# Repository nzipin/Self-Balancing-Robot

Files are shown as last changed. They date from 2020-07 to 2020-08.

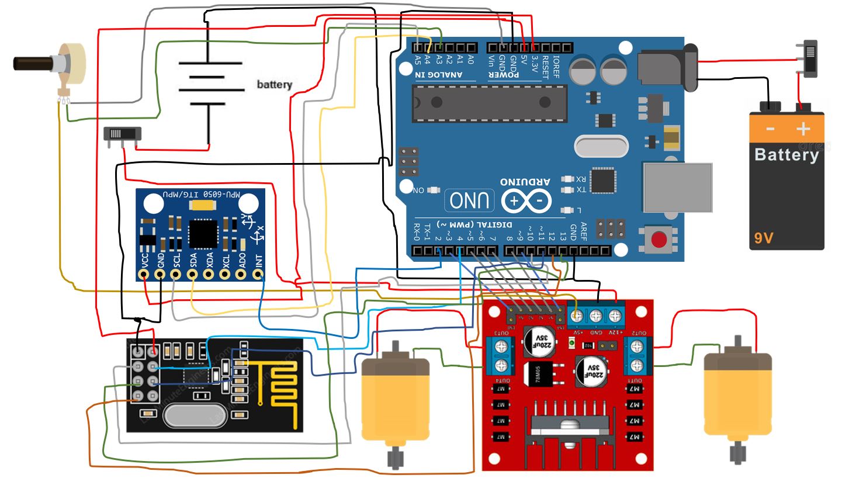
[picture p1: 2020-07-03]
Electronics/Wiring diagram.JPG

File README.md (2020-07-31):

# Self-Balancing-Robot
All artifacts from a 2 wheel balancing robot project as seen on YouTube  
https://www.youtube.com/watch?v=M7D-TyRbdDE&list=PLmEi2OoxXIQ88akwk1nRoXV6LqhXQp3kH  

**Full Parts List**  
*Mechanics:*  
- 1x verntech 4pcs 300mm T Type Aluminum Profile Extrusion https://www.amazon.com/gp/product/B07KB1HD8T/ref=ppx_yo_dt_b_asin_title_o03_s04?ie=UTF8&psc=1  
- 1x Polycarbonate Clear Plastic Sheet 12" X 18" X 0.0625" (1/16") https://www.amazon.com/gp/product/B07MQTDF4R/ref=ppx_yo_dt_b_asin_title_o03_s03?ie=UTF8&psc=1  
- 1x M3 T Slot Nut Hammer Head Fastener Nut https://www.amazon.com/gp/product/B07SDFCTD4/ref=ppx_yo_dt_b_asin_title_o03_s05?ie=UTF8&psc=1  
- 1x 20 Pcs M3 Stainless Steel 304 Hex Socket Head Cap Screws Nuts https://www.amazon.com/gp/product/B07HQ5761L/ref=ppx_yo_dt_b_asin_title_o03_s02?ie=UTF8&psc=1  
- 2x 156:1 Metal Gearmotor 20Dx44L mm 12V CB with Extended Motor Shaft https://www.pololu.com/product/3492  
- 1x Dagu Wild Thumper Wheel 120x60mm Pair with 4mm Shaft Adapters https://www.pololu.com/product/1555  
- 1x Generic plastic coat hanger  

*Electronics:*  
(Robot):  
- 1x Arduino Uno https://www.amazon.com/ELEGOO-Board-ATmega328P-ATMEGA16U2-Compliant/dp/B01EWOE0UU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  
- 1x Silicon Wire https://www.amazon.com/gp/product/B07G2HFCS1/ref=ppx_yo_dt_b_asin_title_o06_s00?ie=UTF8&psc=1  
- 1x Tegg 2PCS 9V Battery Holder with ON/Off Switch https://www.amazon.com/gp/product/B07SSY6LRB/ref=ppx_yo_dt_b_asin_title_o03_s00?ie=UTF8&psc=1  
- 1x M3 Male Female Nylon Hex https://www.amazon.com/gp/product/B07D7828LC/ref=ppx_yo_dt_b_asin_title_o03_s01?ie=UTF8&psc=1  
- 1x 4pcs NRF24L01+ Wireless Transceiver Module2.4G https://www.amazon.com/gp/product/B00LX47OCY/ref=ppx_yo_dt_b_asin_title_o03_s02?ie=UTF8&psc=1  
- 1x 5 Pcs 10K OHM Linear Taper Rotary Potentiometer https://www.amazon.com/gp/product/B01DKCUVMQ/ref=ppx_yo_dt_b_asin_title_o03_s03?ie=UTF8&psc=1  
- 1x 6cm x 4cm proto-PCB https://www.amazon.com/gp/product/B07FFDFLZ3/ref=ppx_yo_dt_b_asin_title_o03_s05?ie=UTF8&psc=1  
- 1x L298N Motor Drive Controller Board https://www.amazon.com/gp/product/B01M29YK5U/ref=ppx_yo_dt_b_asin_title_o03_s05?ie=UTF8&psc=1  
- 1x 3 x 3.7V Battery Holder https://www.amazon.com/gp/product/B071ZQ2X2T/ref=ppx_yo_dt_b_asin_title_o03_s05?ie=UTF8&psc=1  
- 1x MPU6050 3 Axis Accelerometer Gyroscope Module 6 DOF 6-axis Accelerometer Gyroscope Sensor https://www.amazon.com/gp/product/B00LP25V1A/ref=ppx_yo_dt_b_asin_title_o06_s01?ie=UTF8&psc=1  
- 3x 18650 Li-ion Battery  

(Remote Control):  

- 1x Joystick Breakout Module Game Controller for Arduino PS2 https://www.amazon.com/gp/product/B01N59MK0U/ref=ppx_yo_dt_b_asin_title_o01_s00?ie=UTF8&psc=1  
- 1x Arduino Nano https://www.amazon.com/gp/product/B07G99NNXL/ref=ppx_yo_dt_b_asin_title_o01_s01?ie=UTF8&psc=1  
- 1x  3 Pins Mini Toggle Switch https://www.amazon.com/gp/product/B01BWL7Z44/ref=ppx_yo_dt_b_asin_title_o01_s01?ie=UTF8&psc=1  
- incl. 9V battery holder, NRF24L01, and protoboard from robot electronics

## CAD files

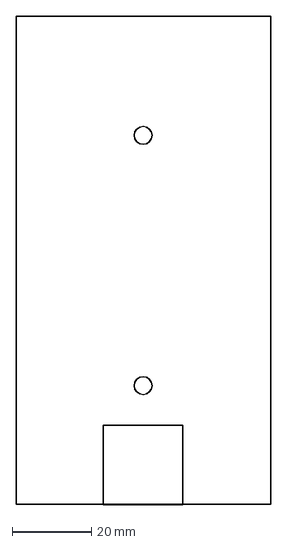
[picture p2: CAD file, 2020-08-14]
Mechanics/CAD/topplate.dxf
64.2 x 123.1 mm

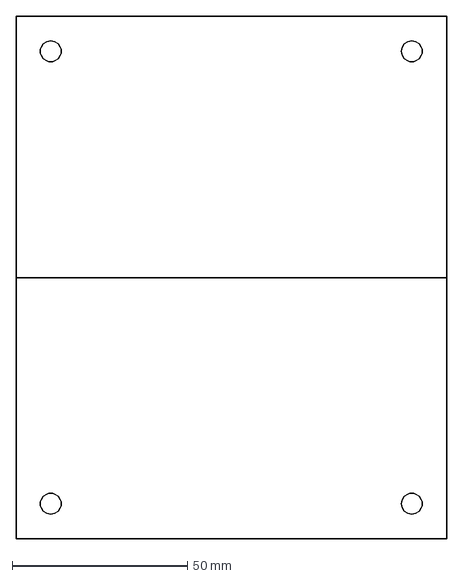
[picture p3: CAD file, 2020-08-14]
Mechanics/CAD/backplate.dxf
123.0 x 149.2 mm

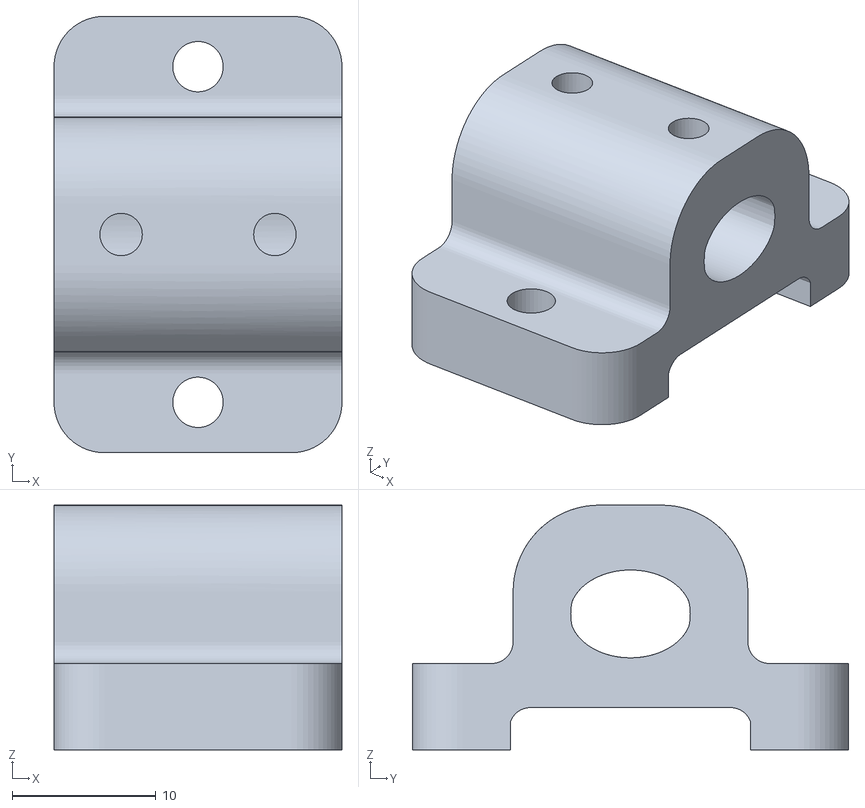
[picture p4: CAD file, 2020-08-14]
Mechanics/CAD/hanger mount.stl
20.0 x 30.3 x 17.0

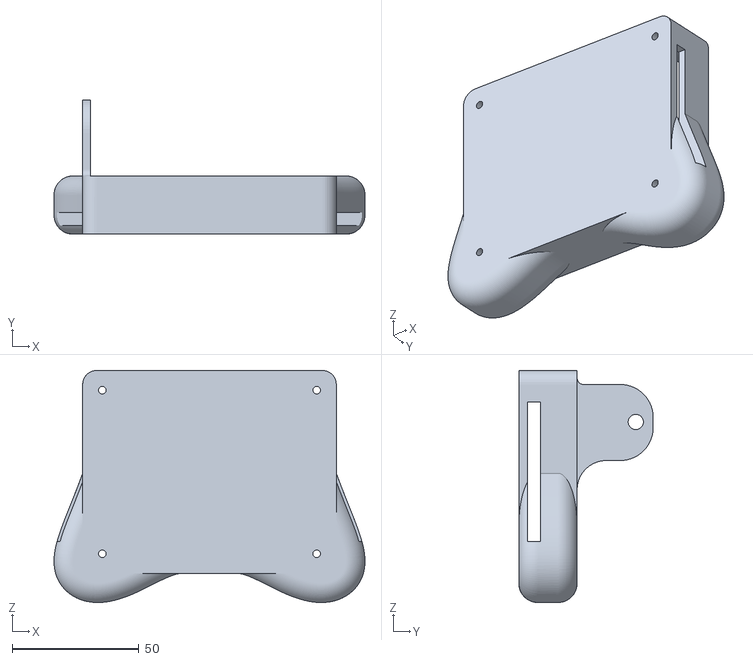
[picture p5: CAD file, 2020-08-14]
Mechanics/CAD/Remote control v1.stl
122.6 x 53.0 x 91.5

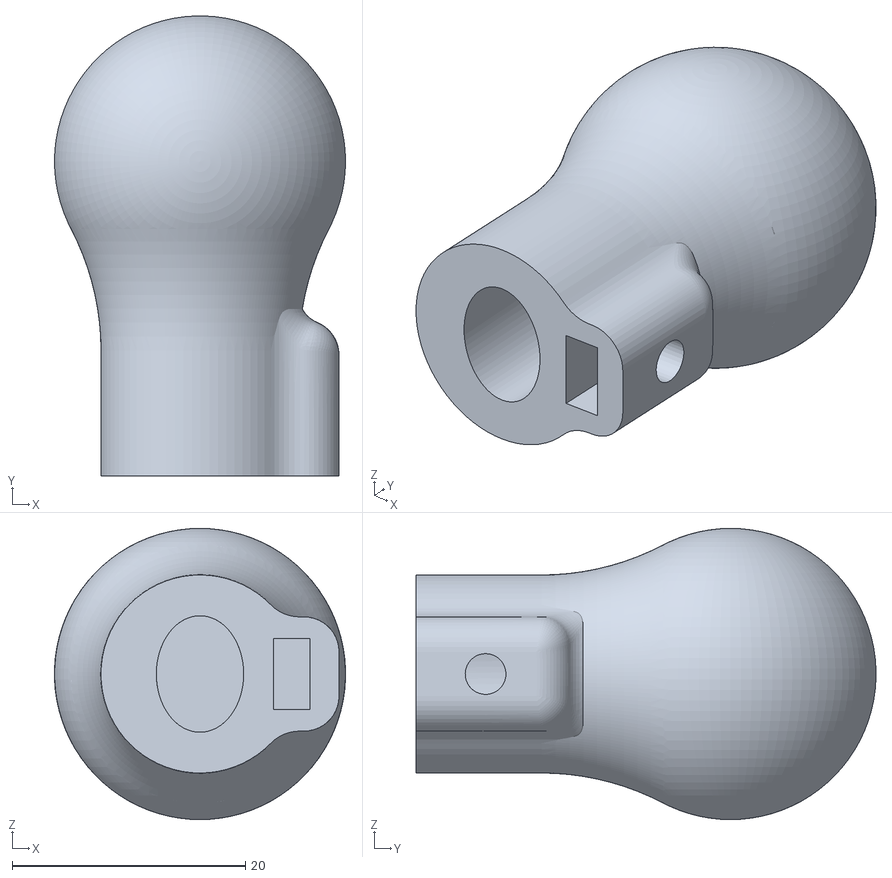
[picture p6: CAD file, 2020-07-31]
Mechanics/CAD/Coat hanger end-piece.stl
25.0 x 39.5 x 25.0

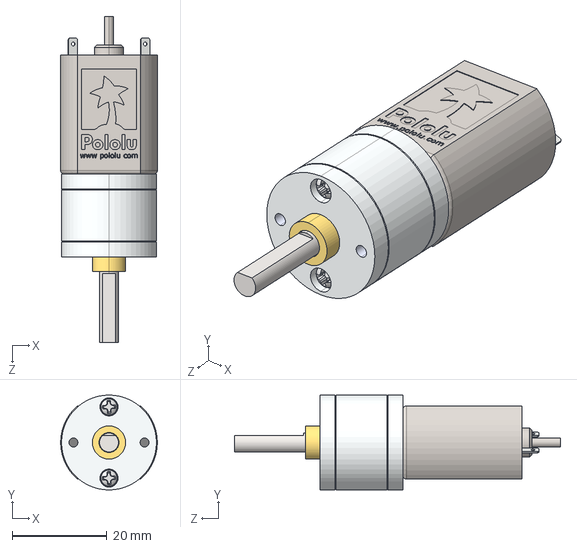
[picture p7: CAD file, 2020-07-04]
Mechanics/CAD/20d-metal-gearmotor-63-78-with-extended-motor-shaft.step
20.4 x 20.0 x 68.7 mm

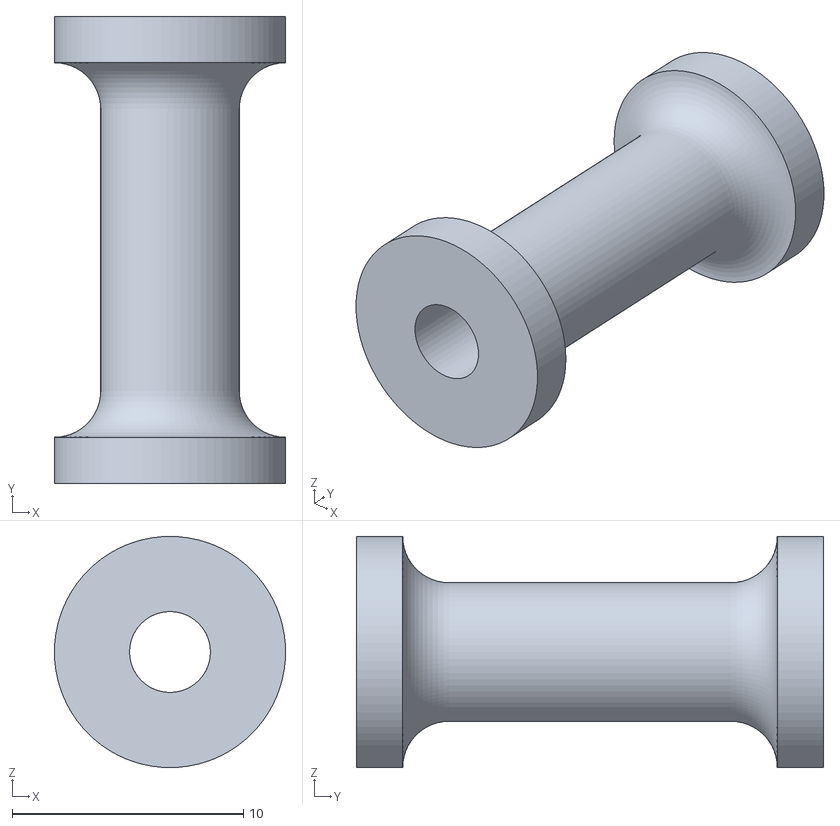
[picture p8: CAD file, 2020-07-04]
Mechanics/CAD/Sapcer v2.stl
10.0 x 20.2 x 10.0

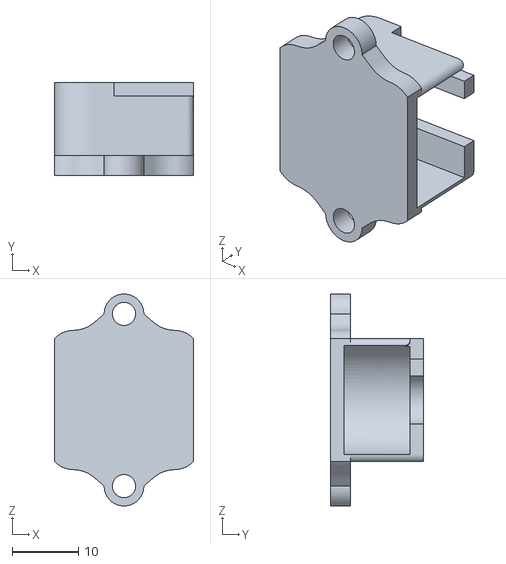
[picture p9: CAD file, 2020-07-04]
Mechanics/CAD/pot mount v3.stl
21.0 x 14.0 x 32.0

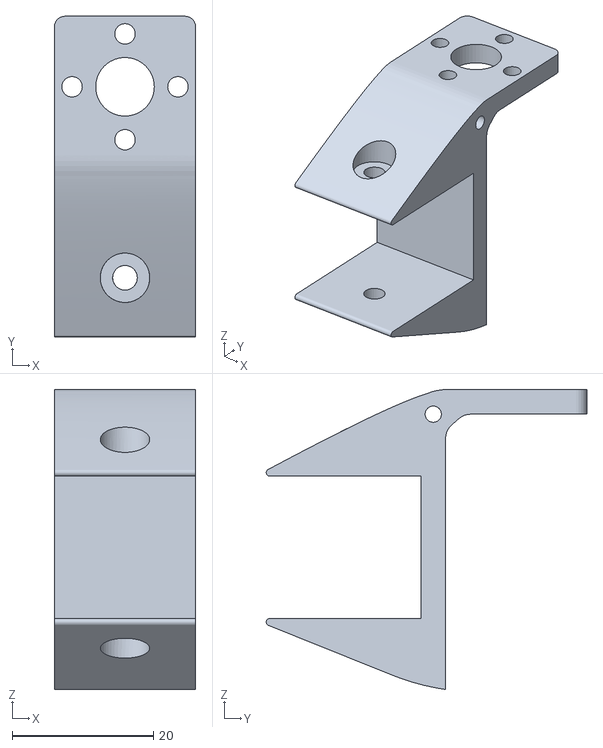
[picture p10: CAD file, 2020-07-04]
Mechanics/CAD/motor bracket v18.stl
20.0 x 45.4 x 42.5

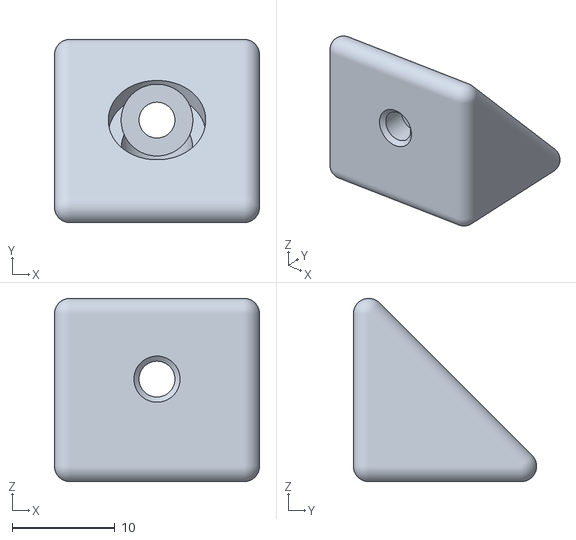
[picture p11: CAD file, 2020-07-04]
Mechanics/CAD/Corner Bracket .stl
20.0 x 17.9 x 17.9

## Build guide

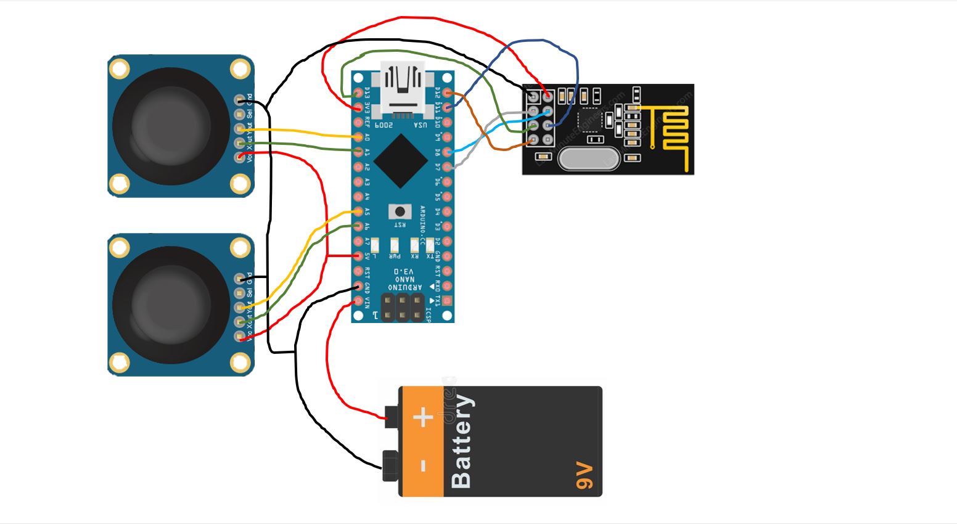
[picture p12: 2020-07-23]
Electronics/Wiring remote.JPG

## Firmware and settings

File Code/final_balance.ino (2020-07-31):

/********** PID **********/
#include <PID_v1.h>

double kP = 24;
double kI = 350;
double kD = 1.2;

double setpoint, input, output;   // PID variables
PID pid(&input, &output, &setpoint, kP, kI, kD, DIRECT); // PID setup

/********** radio **********/
#include <nRF24L01.h>
#include <SPI.h>
#include <RF24.h>
#include <nRF24L01.h>

RF24 radio(10, 4);    // CE, CSN
const byte address[6] = "00001";
float angleV = 0, turnV = 0; // values from remote
float controlValues[2]; // array to receive both data values

/********** L298N **********/
#include <L298N.h>

// Pin definition
const unsigned int EN_A = 3;
const unsigned int IN1_A = 5;
const unsigned int IN2_A = 6;

const unsigned int IN1_B = 7;
const unsigned int IN2_B = 8;
const unsigned int EN_B = 9;

// Create motor instances
L298N rightMotor(EN_A, IN1_A, IN2_A);
L298N leftMotor(EN_B, IN1_B, IN2_B);

// motor speeds
int speedLeft = 0;
int speedRight = 0;

/********** MPU **********/
#include "I2Cdev.h"
#include "MPU6050_6Axis_MotionApps20.h"
#include "Wire.h"

// class default I2C address is 0x68
// specific I2C addresses may be passed as a parameter here
// AD0 low = 0x68 (default for SparkFun breakout and InvenSense evaluation board)
// AD0 high = 0x69
MPU6050 mpu;
//MPU6050 mpu(0x69); // <-- use for AD0 high

#define LED_PIN 13 // (Arduino is 13, Teensy is 11, Teensy++ is 6)
bool blinkState = false;

// MPU control/status vars
bool dmpReady = false;  // set true if DMP init was successful
uint8_t mpuIntStatus;   // holds actual interrupt status byte from MPU
uint8_t devStatus;      // return status after each device operation (0 = success, !0 = error)
uint16_t packetSize;    // expected DMP packet size (default is 42 bytes)
uint16_t fifoCount;     // count of all bytes currently in FIFO
uint8_t fifoBuffer[64]; // FIFO storage buffer

// orientation/motion vars
Quaternion q;           // [w, x, y, z]         quaternion container
VectorInt16 aa;         // [x, y, z]            accel sensor measurements
VectorInt16 aaReal;     // [x, y, z]            gravity-free accel sensor measurements
VectorInt16 aaWorld;    // [x, y, z]            world-frame accel sensor measurements
VectorFloat gravity;    // [x, y, z]            gravity vector
float euler[3];         // [psi, theta, phi]    Euler angle container
float ypr[3];           // [yaw, pitch, roll]   yaw/pitch/roll container and gravity vector

float pitch;
long velocity;

float trimPot;
float trimAngle;

int IMUdataReady = 0;
volatile bool mpuInterrupt = false;

/********** SETUP **********/
void setup() {
    // join I2C bus (I2Cdev library doesn't do this automatically)
    #if I2CDEV_IMPLEMENTATION == I2CDEV_ARDUINO_WIRE
        Wire.begin();
        Wire.setClock(400000); // 400kHz I2C clock. Comment this line if having compilation difficulties
    #elif I2CDEV_IMPLEMENTATION == I2CDEV_BUILTIN_FASTWIRE
        Fastwire::setup(400, true);
    #endif

    Serial.begin(115200);

    // initialize device
    mpu.initialize();
    devStatus = mpu.dmpInitialize();

    // supply your own gyro offsets here, scaled for min sensitivity
    mpu.setXGyroOffset(220);
    mpu.setYGyroOffset(76);
    mpu.setZGyroOffset(-85);
    mpu.setZAccelOffset(1788); // 1688 factory default for my test chip

    // make sure it worked (returns 0 if so)
    if (devStatus == 0) {
        // turn on the DMP, now that it's ready
        mpu.setDMPEnabled(true);

        // enable Arduino interrupt detection
        attachInterrupt(0, dmpDataReady, RISING);
        mpuIntStatus = mpu.getIntStatus();

        // get expected DMP packet size for later comparison
        packetSize = mpu.dmpGetFIFOPacketSize();
    } else {
        // ERROR!
        // 1 = initial memory load failed
        // 2 = DMP configuration updates failed
        // (if it's going to break, usually the code will be 1)
        Serial.print(F("DMP Initialization failed (code "));
        Serial.print(devStatus);
        Serial.println(F(")"));
    }
    
    pid.SetMode(AUTOMATIC);
    pid.SetOutputLimits(-255,255);
    pid.SetSampleTime(10);
    
    pinMode(LED_PIN, OUTPUT);

    radio.begin();
    radio.openReadingPipe(0, address);
    radio.setPALevel(RF24_PA_MIN);
    radio.startListening();
}

void loop() {
  
  // only read remote data if remote is available, otherwise balance normally
  if (radio.available()) {
    radio.read(&controlValues, sizeof(controlValues)); // read values of array
    
    angleV = controlValues[0]; // assign array values to control variables
    turnV = controlValues[1];
  } 
  
  trimPot = analogRead(A3)*-1; // read dial on robot and *-1 for direction

  trimAngle = (trimPot/100) + 5 + angleV; // adjust to degrees

  if (IMUdataReady == 1) {
    readAngles();
  }

  pitch = (ypr[1] * 180/M_PI); // adjust to degrees

  if (abs(turnV) < 15) { // turnV threshold
    turnV = 0;
  }

  if (abs(angleV) < .17) { // angleV threshold
    angleV = 0;
  }

  // PID vars
  setpoint = trimAngle + angleV; 
  input = pitch;

  pid.Compute();

  // set motor speed with adjusted turn values
  speedLeft = output -  turnV;
  speedRight = output + turnV;
  
  if (pitch > 25 || pitch < -25) { // angle threshold
    leftMotor.setSpeed(0);
    rightMotor.setSpeed(0); 
  } else {
    leftMotor.setSpeed(abs(speedLeft));
    rightMotor.setSpeed(abs(speedRight));
  }

  // move motors
  if (speedLeft < 0) { 
    leftMotor.forward();
  } else {
    leftMotor.backward();
  }
  
  if (speedRight < 0) { 
    rightMotor.forward();
  } else {
    rightMotor.backward();
  }
  
  // print some control info
  Serial.print("pitch: ");
  Serial.print(pitch);
  Serial.print(" , trimPot: ");
  Serial.print(trimPot);
  Serial.print(" , angleV: ");
  Serial.print(angleV);
  Serial.print(" , turnV: ");
  Serial.println(turnV);

}

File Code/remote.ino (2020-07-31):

#include <SPI.h>
#include <nRF24L01.h>
#include <RF24.h>

RF24 radio(7, 8); // CE, CSN
const byte address[6] = "00001";
float controlValues[2];

void setup() {
  Serial.begin(9600);
  radio.begin();
  radio.openWritingPipe(address);
  radio.setPALevel(RF24_PA_MIN);
  radio.stopListening();
}
void loop() {
  int forwardValue = analogRead(A1);
  int turnValue = analogRead(A5);

  int mapVal1 = map(forwardValue, 0, 1023, -512, 512);
  float angleValue = (float) mapVal1/200;

  int mapVal2 = map(turnValue, 0, 1023, -512, 512);
  float turnAngleValue = (float) mapVal2/5;

  controlValues[0] = angleValue;
  controlValues[1] = turnAngleValue;
 
  radio.write(&controlValues, sizeof(controlValues));
  
  Serial.print("forward: ");
  Serial.print(angleValue);
  Serial.print( " turn: ");
  Serial.println(turnAngleValue);
}
